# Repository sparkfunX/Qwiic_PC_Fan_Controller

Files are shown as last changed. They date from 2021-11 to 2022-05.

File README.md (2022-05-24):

Qwiic PC Fan Controller
========================================

Qwiic PC Fan Controller

[*Qwiic PC Fan Controller (SPX-18570)*](https://www.sparkfun.com/products/18570)

Whether for active cooling or ventilation, a tiny fan can make a big difference. And by that logic a big fan can make an even bigger difference! Luckily, 4-Wire PC cooling fans come in all shapes and sizes, so there's definitely one out there that's perfect for your project. The only downside is that they can be a pain to drive if you don't need them to be 100% on the throttle all the time. To remedy this, we've modified our Qwiic Blower Fan board to drive any 3- or 4-wire PC Fan with any voltage from 5 to 20VDC!

The Qwiic PC Fan Controller allows you easily control almost any PC fan over the Qwiic bus using the on board ATtiny microcontroller and control firmware. The control firmware monitors the tachometer output of the fan in order to implement PI Control over the fan speed, allowing you to set your desired speed in real units. It's also possible to disable the PI control loop and set the speed as a proportion of the maximum. The accompanying Arduino library includes example code for controlling the fan, tweaking settings, and even setting the fan speed based on an attached Qwiic Temperature Sensor and a lookup table. The on board trimpots allow you to very quickly tune the PI loop parameters to your application, but they can also be overridden by the Qwiic bus for remote configuration.

Heads Up! Without any external power supply connected, the Qwiic PC Fan Controller will attempt to drive the connected fan from the Qwiic bus. Even a very small 5V fan operates at the upper limit of the Qwiic bus' power delivery capability. If there are few other devices on the bus and the fan is not allowed to rapidly change throttle, it is possible to power a small fan directly from the bus. In most applications, however, it will be necessary to provide the PC Fan Controller with a dedicated fan power supply.

Repository Contents
-------------------

* **/Firmware** - Control firmware for the ATtiny
* **/Hardware** - Eagle design files (.brd, .sch)
* **/Production** - Panelized hardware files for production

License Information
-------------------

This product is _**open source**_! 

Please review the LICENSE.md file for license information. 

If you have any questions or concerns on licensing, please contact technical support on our [SparkFun forums](https://forum.sparkfun.com/viewforum.php?f=152).

Distributed as-is; no warranty is given.

- Your friends at SparkFun.

_<COLLABORATION CREDIT>_

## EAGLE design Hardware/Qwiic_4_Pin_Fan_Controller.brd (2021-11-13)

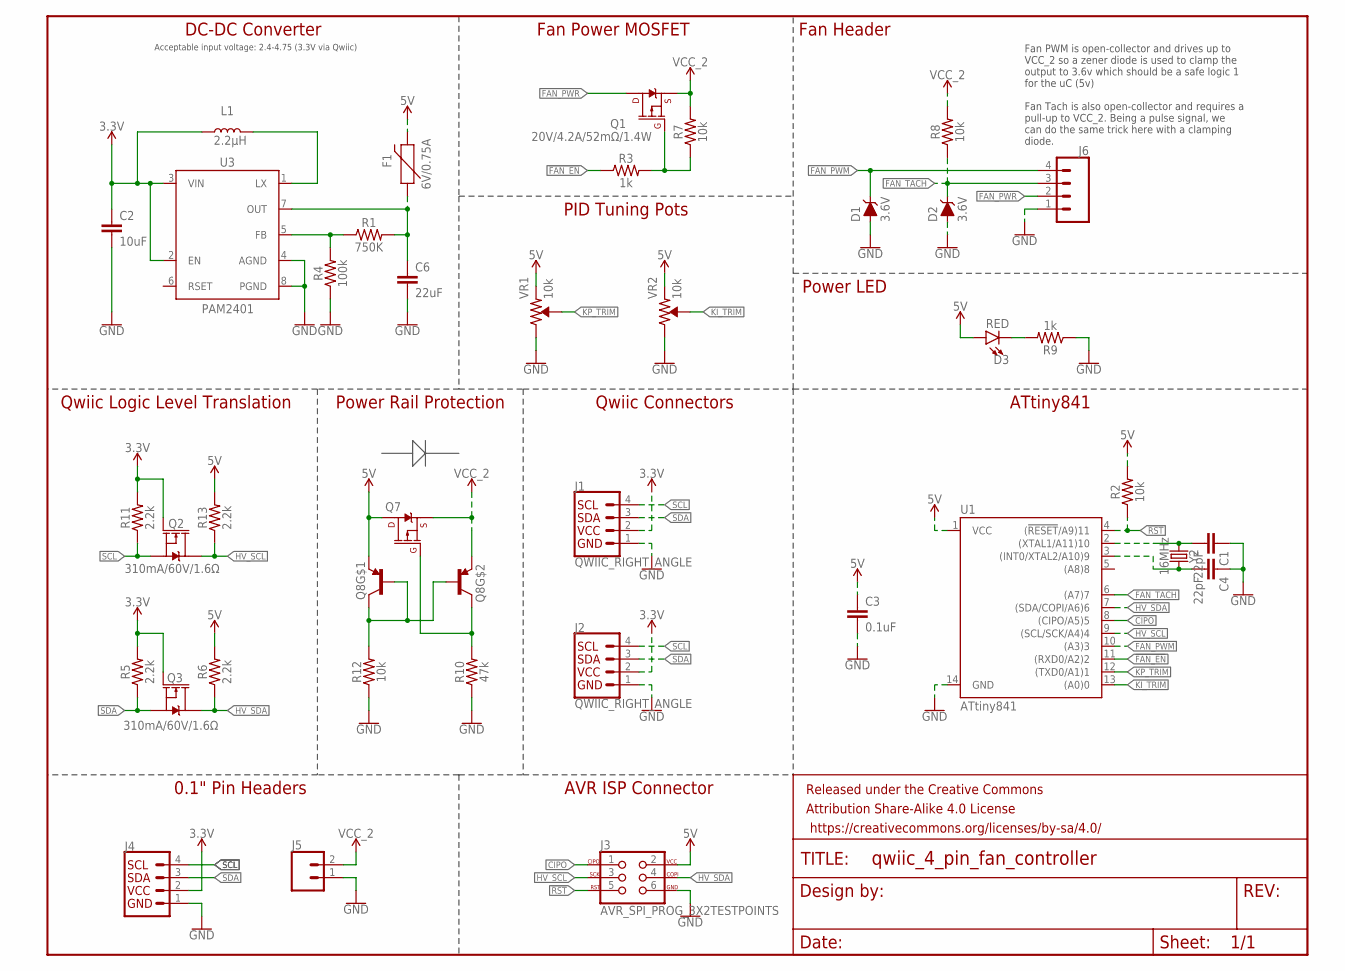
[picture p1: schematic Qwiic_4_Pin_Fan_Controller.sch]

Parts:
C1, C4: 22pF; 0603
C2: 10uF; 0603
C3: 0.1uF; 0603
C6: 22uF; 0805
D1, D2: 3.6V; SOD-323
D3: RED; LED-0603
F1: 6V/0.75A; 1206
FRAME1: FRAME-LETTER; CREATIVE_COMMONS
J1, J2: QWIIC_RIGHT_ANGLE; JST04_1MM_RA
J3: AVR_SPI_PROG_3X2TESTPOINTS; 2X3_TEST_POINTS
J4: I2C_STANDARD_NO_SILK; 1X04_NO_SILK
J5: CONN_021X02_NO_SILK; 1X02_NO_SILK
J6: CONN_041X04_NO_SILK; 1X04_NO_SILK
L1: 2.2μH; 0806
Q1, Q7: 20V/4.2A/52mΩ/1.4W; SOT23-3
Q2, Q3: 310mA/60V/1.6Ω; SOT323
Q8: TRANS_PNP_DUALSOT-363; SOT363_PHILIPS
R1: 750K; 0603
R2, R7, R8, R12: 10k; 0603@1
R3, R9: 1k; 0603
R4: 100k; 0603
R5, R6, R11, R13: 2.2k; 0603
R10: 47k; 0603@1
U1: ATtiny841; SO14
U3: PAM2401; MSOP8
VR1, VR2: 10k; TRIMPOT-SMD-3MM-CLOSED
Y2: 16MHz; CRYSTAL-SMD-2.0X1.6MM

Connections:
3.3V: C2.1, J1.2, J2.2, J4.2, L1.1, Q2.1 (G), Q3.1 (G), R5.2, R11.2, U3.2 (EN), U3.3 (VIN)
5V: C3.1, D3.A, F1.2, J3.2, Q7.3 (D), Q8.1 (E), R2.2, R6.2, R13.2, U1.1 (VCC), VR1.1 (CCW), VR2.1 (CCW)
!FAN_EN: R3.1, U1.11 ((RXD0/A2)2)
!RST: J3.5, R2.1, U1.4 ((!RESET!/A9)11)
CIPO: J3.1, U1.8 ((CIPO/A5)5)
FAN_PWM: D1.C, J6.4, U1.10 ((A3)3)
FAN_PWR: J6.2, Q1.3 (D)
FAN_TACH: D2.C, J6.3, R8.1, U1.6 ((A7)7)
GND: C1.1, C2.2, C3.2, C4.1, C6.2, D1.A, D2.A, J1.1, J2.1, J3.6, J4.1, J5.1, J6.1, R4.1, R9.1, R10.1, R12.1, U1.14 (GND), U3.4 (AGND), U3.8 (PGND), VR1.3 (CW), VR2.3 (CW)
HV_SCL: J3.3, Q2.3 (D), R13.1, U1.9 ((SCL/SCK/A4)4)
HV_SDA: J3.4, Q3.3 (D), R6.1, U1.7 ((SDA/COPI/A6)6)
KI_TRIM: U1.13 ((A0)0), VR2.2 (WIPER)
KP_TRIM: U1.12 ((TXD0/A1)1), VR1.2 (WIPER)
unnamed: C4.2, U1.3 ((INT0/XTAL2/A10)9), Y2.1
unnamed: R1.1, R4.2, U3.5 (FB)
unnamed: L1.2, U3.1 (LX)
unnamed: C1.2, U1.2 ((XTAL1/A11)10), Y2.3 (2)
unnamed: Q1.1 (G), R3.2, R7.1
unnamed: C6.1, F1.1, R1.2, U3.7 (OUT)
unnamed: D3.C, R9.2
unnamed: Q7.1 (G), Q8.3 (C), R10.2
unnamed: Q8.2 (B), Q8.5 (B), Q8.6 (C), R12.2
SCL: J1.4, J2.4, J4.4, Q2.2 (S), R11.1
SDA: J1.3, J2.3, J4.3, Q3.2 (S), R5.1
VCC_2: J5.2, Q1.2 (S), Q7.2 (S), Q8.4 (E), R7.2, R8.2

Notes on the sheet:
DC-DC Converter
Acceptable input voltage: 2.4-4.75 (3.3V via Qwiic)
ATtiny841
Qwiic Connectors
Qwiic Logic Level Translation
0.1" Pin Headers
AVR ISP Connector
Fan Power MOSFET
Fan Header
Fan PWM is open-collector and drives up to VCC_2 so a zener diode is used to clamp the output to 3.6v which should be a safe logic 1 for the uC (5v) Fan Tach is also open-collector and requires a pull-up to VCC_2. Being a pulse signal, we can do the same trick here with a clamping diode.
PID Tuning Pots
Power LED
Power Rail Protection

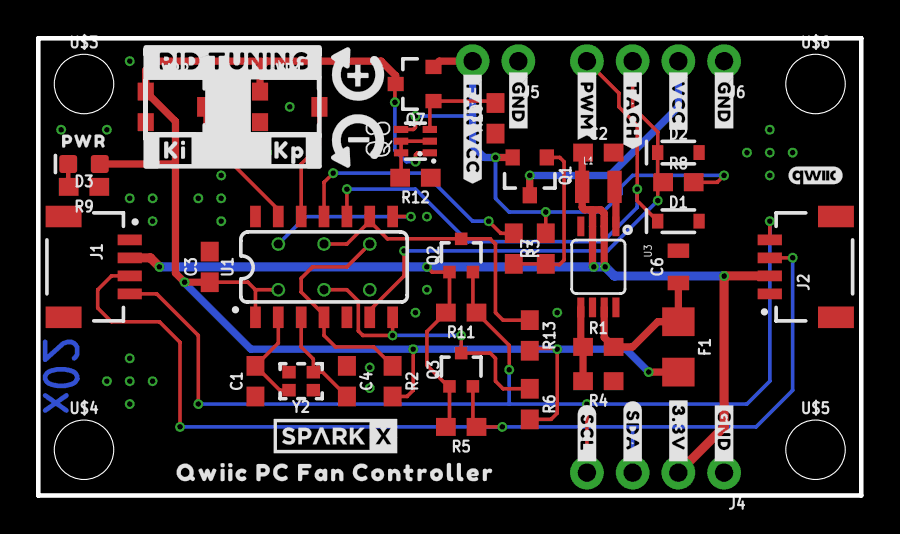
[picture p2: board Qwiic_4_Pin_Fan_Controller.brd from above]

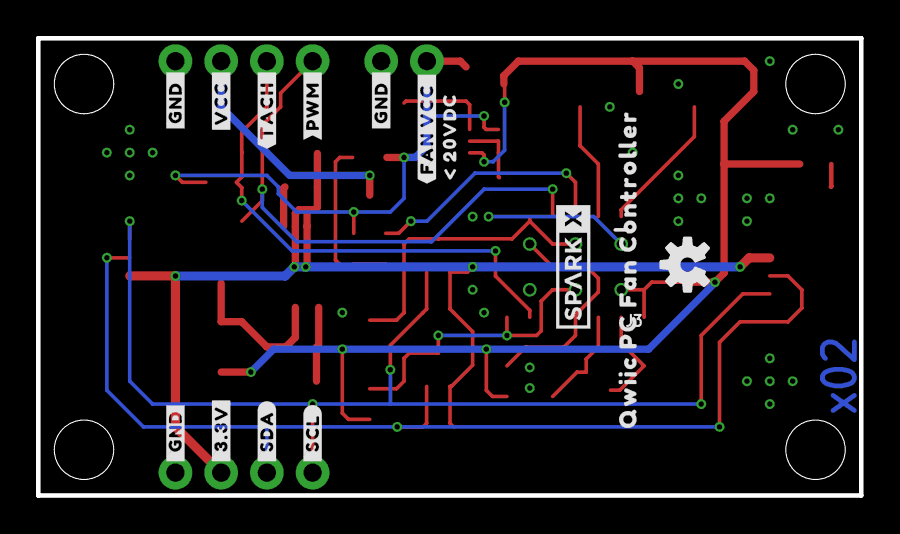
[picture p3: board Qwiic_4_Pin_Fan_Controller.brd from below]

Board: 2 copper layers, 45.7 x 25.4 mm, 76 parts (15 on the bottom side), 25 nets.

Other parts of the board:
U$1, U$9, U$21: #_GND#0
U$2: #_VCC#0
U$3, U$4, U$5, U$6: STAND-OFF
U$7: #_TACH#0
U$8: #_PWM#0
U$10, U$20, U$26: #GND_#0
U$11: #3#3V_#0
U$12: #SDA_#0
U$13: #SCL_#0
U$14: #PID_TUNING0
U$15: KI0
U$16: KP0
U$17: QWIIC_3MM
U$18, U$36: SPARKX-SMALL
U$19: #_FAN_VCC#0
U$22: PWR0
U$23: #VCC_#0
U$24: #TACH_#0
U$25: #PWM_#0
U$27: #_3#3V#0
U$28: #_SDA#0
U$29: #_SCL#0
U$30, U$35: QWIIC_PC_FAN_CONTROLLER0
U$31: #FAN_VCC_#0
U$32: _#_20VDC0
U$37: OSHW-LOGO-S
U$38: TURN_INDICATOR#SVG0

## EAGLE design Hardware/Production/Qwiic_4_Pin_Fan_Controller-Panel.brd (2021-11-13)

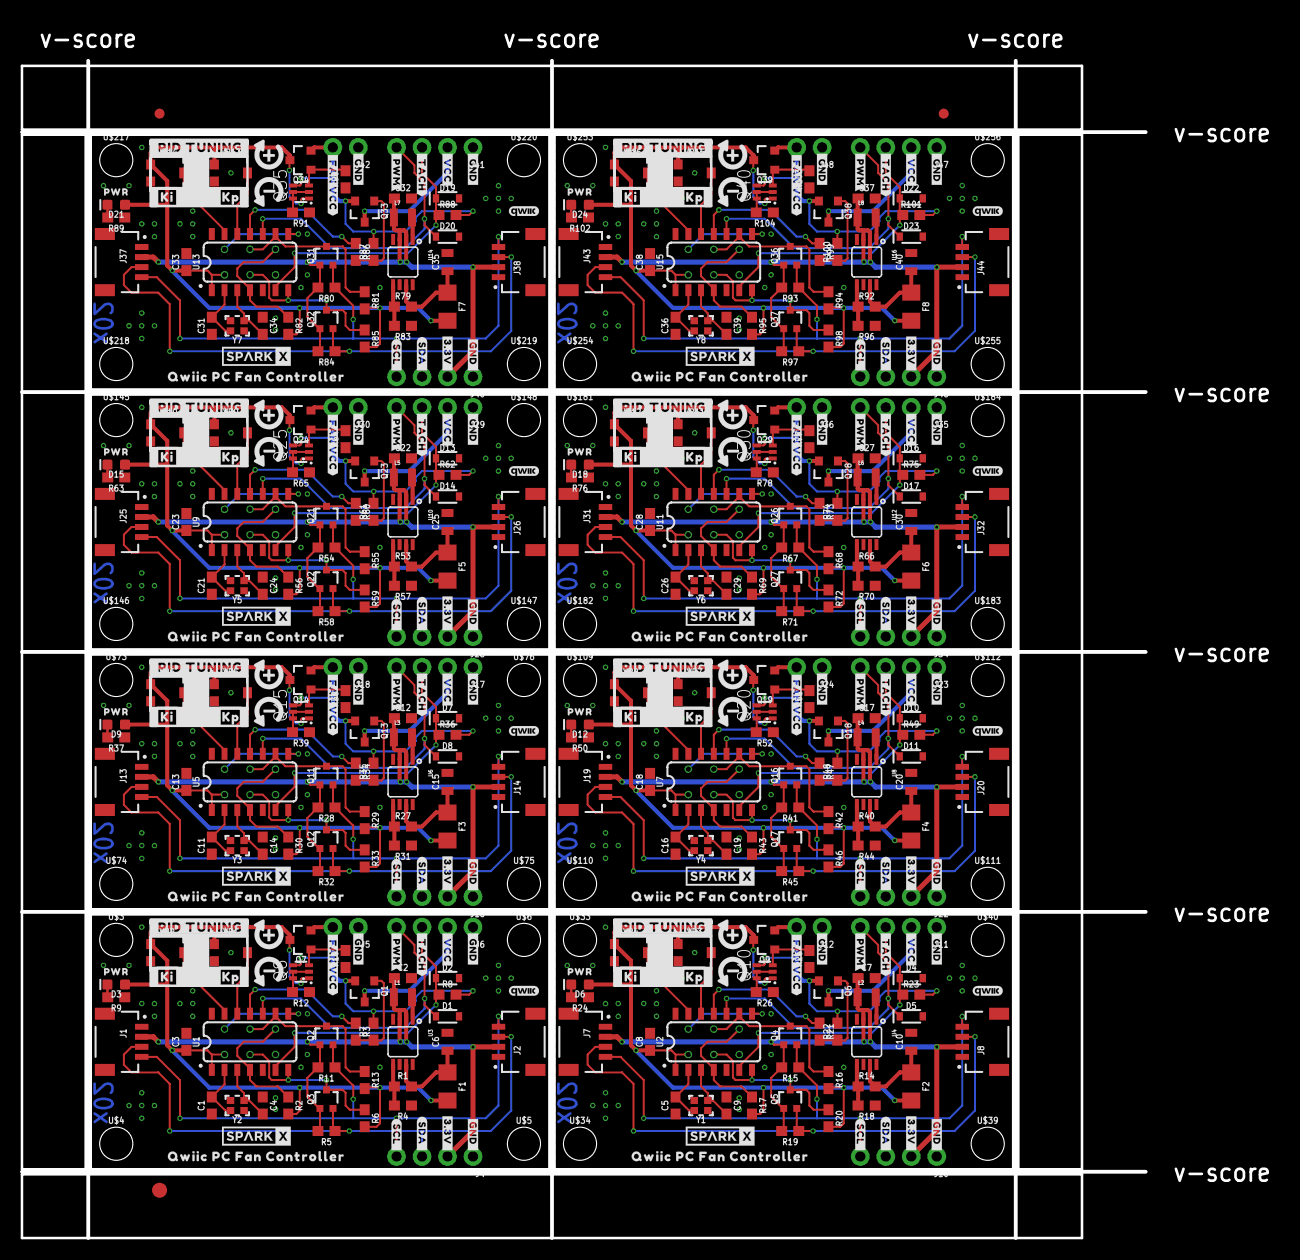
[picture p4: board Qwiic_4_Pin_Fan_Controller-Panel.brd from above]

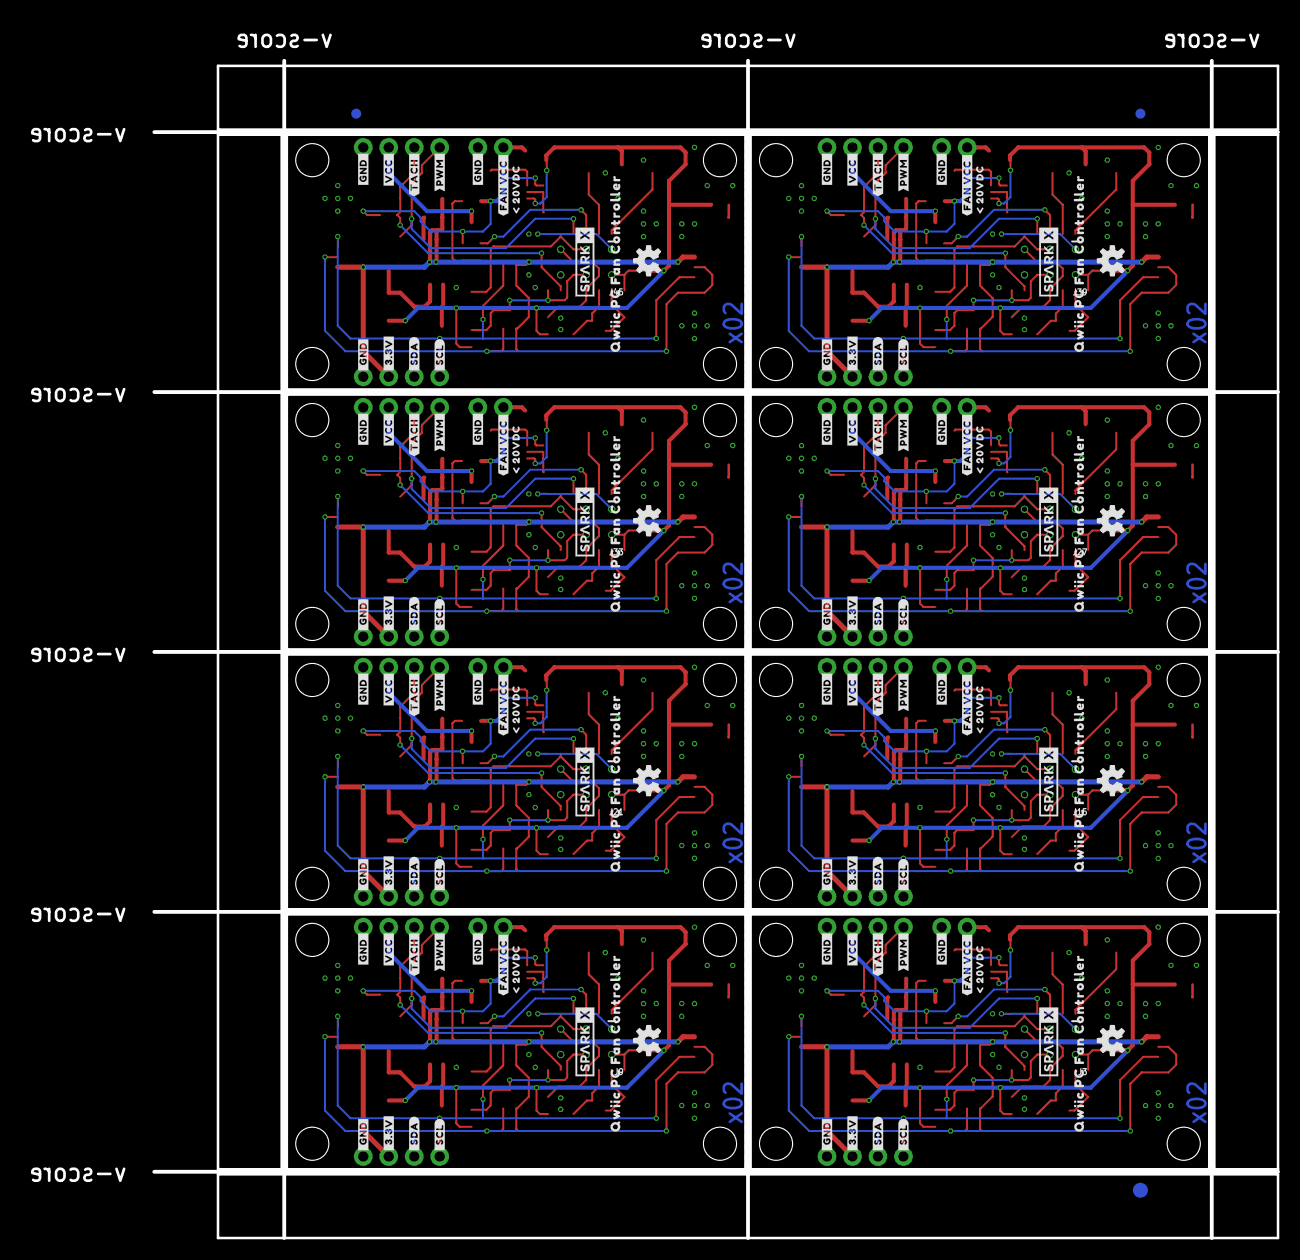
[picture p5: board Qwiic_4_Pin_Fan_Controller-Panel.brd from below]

Board: 2 copper layers, 112.0 x 117.3 mm, 606 parts (123 on the bottom side), 200 nets.

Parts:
C1, C4, C5, C9, C11, C14, C16, C19, C21, C24, C26, C29, C31, C34, C36, C39: 22pF; 0603
C2, C7, C12, C17, C22, C27, C32, C37: 10uF; 0603
C3, C8, C13, C18, C23, C28, C33, C38: 0.1uF; 0603
C6, C10, C15, C20, C25, C30, C35, C40: 22uF; 0805
D1, D2, D4, D5, D7, D8, D10, D11, D13, D14, D16, D17, D19, D20, D22, D23: 3.6V; SOD-323
D3, D6, D9, D12, D15, D18, D21, D24: RED; LED-0603
E$1, E$2, E$3, E$4: FIDUCIAL-1X2
E$5, E$6: FIDUCIAL-1.5X3
F1, F2, F3, F4, F5, F6, F7, F8: 6V/0.75A; 1206
J1, J2, J7, J8, J13, J14, J19, J20, J25, J26, J31, J32, J37, J38, J43, J44: QWIIC_RIGHT_ANGLE; JST04_1MM_RA
J3, J9, J15, J21, J27, J33, J39, J45: AVR_SPI_PROG_3X2TESTPOINTS; 2X3_TEST_POINTS
J4, J6, J10, J11, J16, J17, J22, J23, J28, J29, J34, J35, J40, J41, J46, J47: 1X04_NO_SILK
J5, J12, J18, J24, J30, J36, J42, J48: 1X02_NO_SILK
L1, L2, L3, L4, L5, L6, L7, L8: 2.2μH; 0806
Q1, Q6, Q7, Q9, Q13, Q14, Q18, Q19, Q23, Q24, Q28, Q29, Q33, Q34, Q38, Q39: 20V/4.2A/52mΩ/1.4W; SOT23-3
Q2, Q3, Q4, Q5, Q11, Q12, Q16, Q17, Q21, Q22, Q26, Q27, Q31, Q32, Q36, Q37: 310mA/60V/1.6Ω; SOT323
Q8, Q10, Q15, Q20, Q25, Q30, Q35, Q40: SOT363_PHILIPS
R1, R14, R27, R40, R53, R66, R79, R92: 750K; 0603
R2, R7, R8, R12, R17, R22, R23, R26, R30, R35, R36, R39, R43, R48, R49, R52, R56, R61, R62, R65, R69, R74, R75, R78, R82, R87, R88, R91, R95, R100, R101, R104: 10k; 0603@1
R3, R9, R21, R24, R34, R37, R47, R50, R60, R63, R73, R76, R86, R89, R99, R102: 1k; 0603
R4, R18, R31, R44, R57, R70, R83, R96: 100k; 0603
R5, R6, R11, R13, R15, R16, R19, R20, R28, R29, R32, R33, R41, R42, R45, R46, R54, R55, R58, R59, R67, R68, R71, R72, R80, R81, R84, R85, R93, R94, R97, R98: 2.2k; 0603
R10, R25, R38, R51, R64, R77, R90, R103: 47k; 0603@1
U1, U2, U5, U7, U9, U11, U13, U15: ATtiny841; SO14
U3, U4, U6, U8, U10, U12, U14, U16: PAM2401; MSOP8
U$1, U$9, U$21, U$41, U$45, U$53, U$77, U$81, U$89, U$113, U$117, U$125, U$149, U$153, U$161, U$185, U$189, U$197, U$221, U$225, U$233, U$257, U$261, U$269: #_GND#0
U$2, U$42, U$78, U$114, U$150, U$186, U$222, U$258: #_VCC#0
U$3, U$4, U$5, U$6, U$33, U$34, U$39, U$40, U$73, U$74, U$75, U$76, U$109, U$110, U$111, U$112, U$145, U$146, U$147, U$148, U$181, U$182, U$183, U$184, U$217, U$218, U$219, U$220, U$253, U$254, U$255, U$256: STAND-OFF
U$7, U$43, U$79, U$115, U$151, U$187, U$223, U$259: #_TACH#0
U$8, U$44, U$80, U$116, U$152, U$188, U$224, U$260: #_PWM#0
U$10, U$20, U$26, U$46, U$52, U$57, U$82, U$88, U$93, U$118, U$124, U$129, U$154, U$160, U$165, U$190, U$196, U$201, U$226, U$232, U$237, U$262, U$268, U$273: #GND_#0
U$11, U$47, U$83, U$119, U$155, U$191, U$227, U$263: #3#3V_#0
U$12, U$48, U$84, U$120, U$156, U$192, U$228, U$264: #SDA_#0
U$13, U$49, U$85, U$121, U$157, U$193, U$229, U$265: #SCL_#0
U$14, U$66, U$102, U$138, U$174, U$210, U$246, U$282: #PID_TUNING0
U$15, U$67, U$103, U$139, U$175, U$211, U$247, U$283: KI0
U$16, U$68, U$104, U$140, U$176, U$212, U$248, U$284: KP0
U$17, U$50, U$86, U$122, U$158, U$194, U$230, U$266: QWIIC_3MM
U$18, U$36, U$51, U$62, U$87, U$98, U$123, U$134, U$159, U$170, U$195, U$206, U$231, U$242, U$267, U$278: SPARKX-SMALL
U$19, U$65, U$101, U$137, U$173, U$209, U$245, U$281: #_FAN_VCC#0
U$22, U$69, U$105, U$141, U$177, U$213, U$249, U$285: PWR0
U$23, U$54, U$90, U$126, U$162, U$198, U$234, U$270: #VCC_#0
U$24, U$55, U$91, U$127, U$163, U$199, U$235, U$271: #TACH_#0
U$25, U$56, U$92, U$128, U$164, U$200, U$236, U$272: #PWM_#0
U$27, U$58, U$94, U$130, U$166, U$202, U$238, U$274: #_3#3V#0
U$28, U$59, U$95, U$131, U$167, U$203, U$239, U$275: #_SDA#0
U$29, U$60, U$96, U$132, U$168, U$204, U$240, U$276: #_SCL#0
U$30, U$35, U$61, U$63, U$97, U$99, U$133, U$135, U$169, U$171, U$205, U$207, U$241, U$243, U$277, U$279: QWIIC_PC_FAN_CONTROLLER0
U$31, U$71, U$107, U$143, U$179, U$215, U$251, U$287: #FAN_VCC_#0
U$32, U$72, U$108, U$144, U$180, U$216, U$252, U$288: _#_20VDC0
U$37, U$64, U$100, U$136, U$172, U$208, U$244, U$280: OSHW-LOGO-S
U$38, U$70, U$106, U$142, U$178, U$214, U$250, U$286: TURN_INDICATOR#SVG0
VR1, VR2, VR3, VR4, VR5, VR6, VR7, VR8, VR9, VR10, VR11, VR12, VR13, VR14, VR15, VR16: 10k; TRIMPOT-SMD-3MM-CLOSED
Y1, Y2, Y3, Y4, Y5, Y6, Y7, Y8: 16MHz; CRYSTAL-SMD-2.0X1.6MM

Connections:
3.3V: C2.1, J1.2, J2.2, J4.2, L1.1, Q2.1, Q3.1, R5.2, R11.2, U3.2, U3.3
3.3V1: C7.1, J7.2, J8.2, J10.2, L2.1, Q4.1, Q5.1, R15.2, R19.2, U4.2, U4.3
3.3V2: C12.1, J13.2, J14.2, J16.2, L3.1, Q11.1, Q12.1, R28.2, R32.2, U6.2, U6.3
3.3V3: C17.1, J19.2, J20.2, J22.2, L4.1, Q16.1, Q17.1, R41.2, R45.2, U8.2, U8.3
3.3V4: C22.1, J25.2, J26.2, J28.2, L5.1, Q21.1, Q22.1, R54.2, R58.2, U10.2, U10.3
3.3V5: C27.1, J31.2, J32.2, J34.2, L6.1, Q26.1, Q27.1, R67.2, R71.2, U12.2, U12.3
3.3V6: C32.1, J37.2, J38.2, J40.2, L7.1, Q31.1, Q32.1, R80.2, R84.2, U14.2, U14.3
3.3V7: C37.1, J43.2, J44.2, J46.2, L8.1, Q36.1, Q37.1, R93.2, R97.2, U16.2, U16.3
5V: C3.1, D3.A, F1.2, J3.2, Q7.3, Q8.1, R2.2, R6.2, R13.2, U1.1, VR1.1, VR2.1
5V1: C8.1, D6.A, F2.2, J9.2, Q9.3, Q10.1, R16.2, R17.2, R20.2, U2.1, VR3.1, VR4.1
5V2: C13.1, D9.A, F3.2, J15.2, Q14.3, Q15.1, R29.2, R30.2, R33.2, U5.1, VR5.1, VR6.1
5V3: C18.1, D12.A, F4.2, J21.2, Q19.3, Q20.1, R42.2, R43.2, R46.2, U7.1, VR7.1, VR8.1
5V4: C23.1, D15.A, F5.2, J27.2, Q24.3, Q25.1, R55.2, R56.2, R59.2, U9.1, VR9.1, VR10.1
5V5: C28.1, D18.A, F6.2, J33.2, Q29.3, Q30.1, R68.2, R69.2, R72.2, U11.1, VR11.1, VR12.1
5V6: C33.1, D21.A, F7.2, J39.2, Q34.3, Q35.1, R81.2, R82.2, R85.2, U13.1, VR13.1, VR14.1
5V7: C38.1, D24.A, F8.2, J45.2, Q39.3, Q40.1, R94.2, R95.2, R98.2, U15.1, VR15.1, VR16.1
!FAN_EN: R3.1, U1.11
!FAN_EN1: R21.1, U2.11
!FAN_EN2: R34.1, U5.11
!FAN_EN3: R47.1, U7.11
!FAN_EN4: R60.1, U9.11
!FAN_EN5: R73.1, U11.11
!FAN_EN6: R86.1, U13.11
!FAN_EN7: R99.1, U15.11
!RST: J3.5, R2.1, U1.4
!RST1: J9.5, R17.1, U2.4
!RST2: J15.5, R30.1, U5.4
!RST3: J21.5, R43.1, U7.4
!RST4: J27.5, R56.1, U9.4
!RST5: J33.5, R69.1, U11.4
!RST6: J39.5, R82.1, U13.4
!RST7: J45.5, R95.1, U15.4
CIPO: J3.1, U1.8
CIPO1: J9.1, U2.8
CIPO2: J15.1, U5.8
CIPO3: J21.1, U7.8
CIPO4: J27.1, U9.8
CIPO5: J33.1, U11.8
CIPO6: J39.1, U13.8
CIPO7: J45.1, U15.8
FAN_PWM: D1.C, J6.4, U1.10
FAN_PWM1: D5.C, J11.4, U2.10
FAN_PWM2: D8.C, J17.4, U5.10
FAN_PWM3: D11.C, J23.4, U7.10
FAN_PWM4: D14.C, J29.4, U9.10
FAN_PWM5: D17.C, J35.4, U11.10
FAN_PWM6: D20.C, J41.4, U13.10
FAN_PWM7: D23.C, J47.4, U15.10
FAN_PWR: J6.2, Q1.3
FAN_PWR1: J11.2, Q6.3
FAN_PWR2: J17.2, Q13.3
FAN_PWR3: J23.2, Q18.3
FAN_PWR4: J29.2, Q23.3
FAN_PWR5: J35.2, Q28.3
FAN_PWR6: J41.2, Q33.3
FAN_PWR7: J47.2, Q38.3
FAN_TACH: D2.C, J6.3, R8.1, U1.6
FAN_TACH1: D4.C, J11.3, R23.1, U2.6
FAN_TACH2: D7.C, J17.3, R36.1, U5.6
FAN_TACH3: D10.C, J23.3, R49.1, U7.6
FAN_TACH4: D13.C, J29.3, R62.1, U9.6
FAN_TACH5: D16.C, J35.3, R75.1, U11.6
FAN_TACH6: D19.C, J41.3, R88.1, U13.6
FAN_TACH7: D22.C, J47.3, R101.1, U15.6
GND: C1.1, C2.2, C3.2, C4.1, C6.2, D1.A, D2.A, J1.1, J2.1, J3.6, J4.1, J5.1, J6.1, R4.1, R9.1, R10.1, R12.1, U1.14, U3.4, U3.8, VR1.3, VR2.3
GND1: C5.1, C7.2, C8.2, C9.1, C10.2, D4.A, D5.A, J7.1, J8.1, J9.6, J10.1, J11.1, J12.1, R18.1, R24.1, R25.1, R26.1, U2.14, U4.4, U4.8, VR3.3, VR4.3
GND2: C11.1, C12.2, C13.2, C14.1, C15.2, D7.A, D8.A, J13.1, J14.1, J15.6, J16.1, J17.1, J18.1, R31.1, R37.1, R38.1, R39.1, U5.14, U6.4, U6.8, VR5.3, VR6.3
GND3: C16.1, C17.2, C18.2, C19.1, C20.2, D10.A, D11.A, J19.1, J20.1, J21.6, J22.1, J23.1, J24.1, R44.1, R50.1, R51.1, R52.1, U7.14, U8.4, U8.8, VR7.3, VR8.3
GND4: C21.1, C22.2, C23.2, C24.1, C25.2, D13.A, D14.A, J25.1, J26.1, J27.6, J28.1, J29.1, J30.1, R57.1, R63.1, R64.1, R65.1, U9.14, U10.4, U10.8, VR9.3, VR10.3
GND5: C26.1, C27.2, C28.2, C29.1, C30.2, D16.A, D17.A, J31.1, J32.1, J33.6, J34.1, J35.1, J36.1, R70.1, R76.1, R77.1, R78.1, U11.14, U12.4, U12.8, VR11.3, VR12.3
GND6: C31.1, C32.2, C33.2, C34.1, C35.2, D19.A, D20.A, J37.1, J38.1, J39.6, J40.1, J41.1, J42.1, R83.1, R89.1, R90.1, R91.1, U13.14, U14.4, U14.8, VR13.3, VR14.3
GND7: C36.1, C37.2, C38.2, C39.1, C40.2, D22.A, D23.A, J43.1, J44.1, J45.6, J46.1, J47.1, J48.1, R96.1, R102.1, R103.1, R104.1, U15.14, U16.4, U16.8, VR15.3, VR16.3
HV_SCL: J3.3, Q2.3, R13.1, U1.9
HV_SCL1: J9.3, Q4.3, R16.1, U2.9
HV_SCL2: J15.3, Q11.3, R29.1, U5.9
HV_SCL3: J21.3, Q16.3, R42.1, U7.9
HV_SCL4: J27.3, Q21.3, R55.1, U9.9
HV_SCL5: J33.3, Q26.3, R68.1, U11.9
HV_SCL6: J39.3, Q31.3, R81.1, U13.9
HV_SCL7: J45.3, Q36.3, R94.1, U15.9
HV_SDA: J3.4, Q3.3, R6.1, U1.7
HV_SDA1: J9.4, Q5.3, R20.1, U2.7
HV_SDA2: J15.4, Q12.3, R33.1, U5.7
HV_SDA3: J21.4, Q17.3, R46.1, U7.7
HV_SDA4: J27.4, Q22.3, R59.1, U9.7
HV_SDA5: J33.4, Q27.3, R72.1, U11.7
HV_SDA6: J39.4, Q32.3, R85.1, U13.7
HV_SDA7: J45.4, Q37.3, R98.1, U15.7
KI_TRIM: U1.13, VR2.2
KI_TRIM1: U2.13, VR4.2
KI_TRIM2: U5.13, VR6.2
KI_TRIM3: U7.13, VR8.2
KI_TRIM4: U9.13, VR10.2
KI_TRIM5: U11.13, VR12.2
KI_TRIM6: U13.13, VR14.2
KI_TRIM7: U15.13, VR16.2
KP_TRIM: U1.12, VR1.2
KP_TRIM1: U2.12, VR3.2
KP_TRIM2: U5.12, VR5.2
KP_TRIM3: U7.12, VR7.2
KP_TRIM4: U9.12, VR9.2
KP_TRIM5: U11.12, VR11.2
KP_TRIM6: U13.12, VR13.2
KP_TRIM7: U15.12, VR15.2
unnamed: C4.2, U1.3, Y2.1
unnamed: R1.1, R4.2, U3.5
unnamed: L1.2, U3.1
unnamed: C1.2, U1.2, Y2.3
unnamed: Q1.1, R3.2, R7.1
unnamed: C6.1, F1.1, R1.2, U3.7
unnamed: D3.C, R9.2
unnamed: R14.1, R18.2, U4.5
unnamed: L2.2, U4.1
unnamed: C9.2, U2.3, Y1.1
unnamed: C5.2, U2.2, Y1.3
unnamed: Q6.1, R21.2, R22.1
unnamed: C10.1, F2.1, R14.2, U4.7
unnamed: D6.C, R24.2
unnamed: Q7.1, Q8.3, R10.2
unnamed: Q8.2, Q8.5, Q8.6, R12.2
unnamed: Q9.1, Q10.3, R25.2
unnamed: Q10.2, Q10.5, Q10.6, R26.2
unnamed: R27.1, R31.2, U6.5
unnamed: L3.2, U6.1
unnamed: C14.2, U5.3, Y3.1
unnamed: C11.2, U5.2, Y3.3
unnamed: Q13.1, R34.2, R35.1
unnamed: C15.1, F3.1, R27.2, U6.7
unnamed: D9.C, R37.2
unnamed: Q14.1, Q15.3, R38.2
unnamed: Q15.2, Q15.5, Q15.6, R39.2
unnamed: R40.1, R44.2, U8.5
unnamed: L4.2, U8.1
unnamed: C19.2, U7.3, Y4.1
unnamed: C16.2, U7.2, Y4.3
unnamed: Q18.1, R47.2, R48.1
unnamed: C20.1, F4.1, R40.2, U8.7
unnamed: D12.C, R50.2
unnamed: Q19.1, Q20.3, R51.2
unnamed: Q20.2, Q20.5, Q20.6, R52.2
unnamed: R53.1, R57.2, U10.5
unnamed: L5.2, U10.1
unnamed: C24.2, U9.3, Y5.1
unnamed: C21.2, U9.2, Y5.3
unnamed: Q23.1, R60.2, R61.1
unnamed: C25.1, F5.1, R53.2, U10.7
unnamed: D15.C, R63.2
unnamed: Q24.1, Q25.3, R64.2
unnamed: Q25.2, Q25.5, Q25.6, R65.2
unnamed: R66.1, R70.2, U12.5
unnamed: L6.2, U12.1
unnamed: C29.2, U11.3, Y6.1
unnamed: C26.2, U11.2, Y6.3
unnamed: Q28.1, R73.2, R74.1
unnamed: C30.1, F6.1, R66.2, U12.7
unnamed: D18.C, R76.2
unnamed: Q29.1, Q30.3, R77.2
unnamed: Q30.2, Q30.5, Q30.6, R78.2
unnamed: R79.1, R83.2, U14.5
unnamed: L7.2, U14.1
unnamed: C34.2, U13.3, Y7.1
unnamed: C31.2, U13.2, Y7.3
unnamed: Q33.1, R86.2, R87.1
unnamed: C35.1, F7.1, R79.2, U14.7
unnamed: D21.C, R89.2
unnamed: Q34.1, Q35.3, R90.2
unnamed: Q35.2, Q35.5, Q35.6, R91.2
unnamed: R92.1, R96.2, U16.5
unnamed: L8.2, U16.1
unnamed: C39.2, U15.3, Y8.1
unnamed: C36.2, U15.2, Y8.3
unnamed: Q38.1, R99.2, R100.1
unnamed: C40.1, F8.1, R92.2, U16.7
unnamed: D24.C, R102.2
unnamed: Q39.1, Q40.3, R103.2
unnamed: Q40.2, Q40.5, Q40.6, R104.2
SCL: J1.4, J2.4, J4.4, Q2.2, R11.1
SCL1: J7.4, J8.4, J10.4, Q4.2, R15.1
SCL2: J13.4, J14.4, J16.4, Q11.2, R28.1
SCL3: J19.4, J20.4, J22.4, Q16.2, R41.1
SCL4: J25.4, J26.4, J28.4, Q21.2, R54.1
SCL5: J31.4, J32.4, J34.4, Q26.2, R67.1
SCL6: J37.4, J38.4, J40.4, Q31.2, R80.1
SCL7: J43.4, J44.4, J46.4, Q36.2, R93.1
SDA: J1.3, J2.3, J4.3, Q3.2, R5.1
SDA1: J7.3, J8.3, J10.3, Q5.2, R19.1
SDA2: J13.3, J14.3, J16.3, Q12.2, R32.1
SDA3: J19.3, J20.3, J22.3, Q17.2, R45.1
SDA4: J25.3, J26.3, J28.3, Q22.2, R58.1
SDA5: J31.3, J32.3, J34.3, Q27.2, R71.1
SDA6: J37.3, J38.3, J40.3, Q32.2, R84.1
SDA7: J43.3, J44.3, J46.3, Q37.2, R97.1
VCC_1: J12.2, Q6.2, Q9.2, Q10.4, R22.2, R23.2
VCC_2: J5.2, Q1.2, Q7.2, Q8.4, R7.2, R8.2
VCC_3: J18.2, Q13.2, Q14.2, Q15.4, R35.2, R36.2
VCC_4: J24.2, Q18.2, Q19.2, Q20.4, R48.2, R49.2
VCC_5: J30.2, Q23.2, Q24.2, Q25.4, R61.2, R62.2
VCC_6: J36.2, Q28.2, Q29.2, Q30.4, R74.2, R75.2
VCC_7: J42.2, Q33.2, Q34.2, Q35.4, R87.2, R88.2
VCC_8: J48.2, Q38.2, Q39.2, Q40.4, R100.2, R101.2

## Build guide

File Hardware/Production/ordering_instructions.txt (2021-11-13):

panel size, 106x117mm
PCB thickness, 1.6mm
number of layers, 2
soldermask color, Black
silkscreen color, White
oz copper, 1oz
finish, HASL lead free
stencils, none
pcs per panel, 8
min trace width, 0.2032mm / 0.0080in
min drill size, 0.3000mm / 0.0118in

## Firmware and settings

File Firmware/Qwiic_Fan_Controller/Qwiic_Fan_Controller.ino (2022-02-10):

#include <Wire.h>
#include <EEPROM.h>
#include <PIDController.h> // https://github.com/DonnyCraft1/PIDArduino

/****************************************************
 * HARDWARE CONFIGURATION
 * This firmware is used on multiple boards with minor
 * hardware differences so BE CAREFUL to define the 
 * correct hardware configuration below before 
 * programming!
****************************************************/
#define QWIIC_PC_FAN_CONTROLLER // SPX-18570
//#define QWIIC_BLOWER // SPX-18561

#ifdef QWIIC_PC_FAN_CONTROLLER
#define TRIM_DISABLE_DEFAULT 0x00
#endif
#ifdef QWIIC_BLOWER
#define TRIM_DISABLE_DEFAULT 0xFF
#endif 

/* PIN ASSIGNMENTS */
#define PIN_TRIM_KI 0    // ADC in from trimpot
#define PIN_TRIM_KP 1    // ADC in from trimpot
#define PIN_FAN_ENABLE 2 // DO to !FAN_EN
#define PIN_PWM_OUT 3    // DO to FAN_PWM
#define PIN_TACH_IN 7    // DI from FAN_TACH

/* I²C STUFF */
#define MAX_SENT_BYTES 0x05 // Used to ignore invalid commands
#define DEFAULT_ADDR 0x36   // Factory Default Peripheral Address

/* REGISTER MAP */
#define WIRE_ADDR 0x00             // Device Address
#define FAN_ENABLE 0x01            // Enable power to fan VCC pin (0xFF to enable)
#define SETPOINT_RPM 0x02          // PI Controller setpoint in RPM (2 bytes unsigned integer)
#define KP_VALUE 0x04              // PI Controller Proportional Term (2 bytes signed fixed decimal) \
                                   // Setting this parameter from the I²C Controller overrides the onboard trimpot
#define KI_VALUE 0x06              // PI Controller Integral Term (2 bytes signed fixed decimal) \
                                   // Setting this parameter from the I²C Controller overrides the onboard trimpot
#define FAN_TACH_DIVIDER 0x08      // Pulses per rotation indicated by fan/blower datasheet (usually 2)
#define FAN_ACTUAL_RPM 0x09        // Fan Speed Actual as indicated by Tachometer, input to PI Controller (2 bytes integer)
#define PI_OUT 0x0B                // Output of PI Controller for debugging (2 bytes integer)
#define PI_LOOP_DISABLE 0x0D       // Disable PI Controller and use contents of PROPORTIONAL_THROTTLE as speed (0xFF for Disable)
#define PROPORTIONAL_THROTTLE 0x0E // Fan speed as % of MAX. Inverse of PWM Width Cycle.                          \
                                   // When PI Controller is Enabled this register contains its output x (100/320) \
                                   // Whem PI Controller is Disabled the PWM Width Cycle is set to this register's inverse
#define TRIMMER_SCALE 0x0F         // Trimpot values are multiplied by this number. Probably only useful in edge cases. 2.0 (20) by default.
#define TRIMMER_DISABLE 0x10       // Stop reading trimpot ADCs and only use values written to the Kx_VALUE register by the I²C Controller (0xFF for Disable)
#define FW_VERSION 0x11            // Firmware version 

/* EEPROM MAP */
#define EEPROM_DEV_ADDR 0x00        // Because the I²C device address is user selectable, we need to remember it between boot cycles

/* MISCELLANEOUS GLOBAL VARS */
uint8_t receivedCommands[MAX_SENT_BYTES]; // I²C command buffer
uint8_t wire_addr = DEFAULT_ADDR;         // I²C device address
bool changeFlag = 0;                      // Use this flag to alert the main loop when a register change requires attention
uint8_t registerIndex = 0;                // Use this to track our position in the device registers during consecutive read operations

/****************************************************
 * SET THE REGISTER MAP DEFAULTS
 * These are the bus-accessible device registers
 * and their default values */
uint8_t registerMap[0x12] = 
    {
        0x00,                   // WIRE_ADDR
        0x00,                   // FAN_ENABLE
        0x00,                   // SETPOINT_RPM
        0x00,                   // SETPOINT_RPM BYTE 2
        0,                      // KP_VALUE (70 interpreted as 2.50)
        250,                     // KP_VALUE BYTE 2 
        1,                      // KP_VALUE (390 interpreted as 3.90)
        134,                     // KP_VALUE BYTE 2
        2,                   // FAN_TACH_DIVIDER (2 pulses per rotation)
        0x00,                   // FAN_ACTUAL_RPM 
        0x00,                   // FAN_ACTUAL_RPM BYTE 2
        0x00,                   // PI_OUT
        0x00,                   // PI_OUT BYTE 2
        0x00,                   // PI_LOOP_DISABLE (enabled)
        0x00,                   // PROPORTIONAL_THROTTLE
        20,                   // TRIMMER_SCALE (20 interpreted as 2.0)
        TRIM_DISABLE_DEFAULT,    // TRIMMER_DISABLE
        11                      // FIRMWARE VERSION 1.1
    };
/****************************************************/

// Instantiate PI Controller
PIDController piController;

void setup()
{
    // Check EEPROM for a bus address and set accordingly
    setWireAddress();

    // Setup timers for 25kHz Fast PWM
    fastPWMSetup();

    // Set the initial pin states
    pinMode(PIN_PWM_OUT, OUTPUT);
    pinMode(PIN_TACH_IN, INPUT_PULLUP); // Fan Tachometer is open-collector
    pinMode(PIN_FAN_ENABLE, OUTPUT);
    digitalWrite(PIN_FAN_ENABLE, HIGH); // Fan Enable is active low. Boot disabled to avoid hard start
    pinMode(PIN_TRIM_KI, INPUT);
    pinMode(PIN_TRIM_KP, INPUT);

    // Start I2C
    Wire.begin(wire_addr);
    Wire.onRequest(requestEvent);
    Wire.onReceive(receiveEvent);

    // Start the PI Controller
    piController.begin();
    piController.limit(20, 320); // Limit the PI output to prevent integral windup
}

void loop()
{
    // Get the tachometer reading, turn it into a real RPM using the value from
    // FAN_TACH_DIVIDER, and stuff it into FAN_ACTUAL_RPM for the I²C controller
    // to query and for the PI controller to compute against.
    readTachometer();

    // Finding which device register has been changed and updating
    // the approptiate settings takes some time so we only do it if
    // the registers have been poked. This way, we interfere as little
    // as possible with the PI Controller and PWM Generator
    if (changeFlag)
    {
        updateSettings();
    }

    // If the hardware is a Qwiic 4-Wire Fan Controller and the TRIMMER_DISABLE flag isn't set
    // then read the trimmers, apply the correct scale and offset, and then load those
    // values into the Kx_VALUE registers. If the TRIMMER_DISABLE flag is set, or this is
    // a Qwiic Blower board without trimpots, we skip reading the trimpots, so whatever
    // value is in the Kx_VALUE register from the last I²C receive is used for tuning.
    if (registerMap[TRIMMER_DISABLE] != 0xFF)
    {
        readTrimmers();
    }

    // Check whether the user has disabled the control loop in
    // favor of direct proportional speed control. If so, set
    // the PWM Width according to the contents of PROPORTIONAL_THROTTLE
    // if not, compute the output of the PI controller from the
    // contents of SETPOINT_RPM
    if (registerMap[PI_LOOP_DISABLE] == 0xFF)
    {
        pwmWidth(map(registerMap[PROPORTIONAL_THROTTLE], 0, 100, 0, 320));
    }
    else
    {
        piUpdate();
    }
}

/****************************************************
 * Function piUpdate()
 * The PID library has a 'compute' function, which we do
 * call in this method. However, in our particular case, 
 * it's easier to package that up with the tuning functions
 * becuase we always update our tunings before calculating 
 * the output. It seems excessive but it costs us less time
 * to just update the tunings than it does to check whether
 * it's necessary. We also use this method to update the
 * output value in the register map. 
****************************************************/
void piUpdate()
{

    float proportional = 0;
    float integral = 0;
    uint16_t setpoint = 0;
    uint16_t piOutput = 0;
    uint16_t tachReading = 0;

    // Expand the registerMap values back into int16
    // Multiply by 0.01 as neccessary to move the decimal into
    // the right position
    proportional += registerMap[KP_VALUE] << 8;
    proportional += registerMap[KP_VALUE + 0x01];
    proportional *= 0.01;

    integral += registerMap[KI_VALUE] << 8;
    integral += registerMap[KI_VALUE + 0x01];
    integral *= 0.01;

    setpoint += registerMap[SETPOINT_RPM] << 8;
    setpoint += registerMap[SETPOINT_RPM + 0x01];

    tachReading += registerMap[FAN_ACTUAL_RPM] << 8;
    tachReading += registerMap[FAN_ACTUAL_RPM + 0x01];

    // PC Fans tend to have a dead zone at the low end, so we limit the PI controller
    // to the range above this dead zone (to prevent stalling the fan and setting up
    // an oscillation) This does mean, however, that the PI controller will never 
    // organically output a 0, so if the fan speed is set to 0 we need to override the
    // PI controller
    if(setpoint !=0){

      // Update the PI Controller
      piController.setpoint(setpoint);
      piController.tune(proportional, integral, 0);
      piOutput = piController.compute(tachReading);

    }else{

      piOutput = 0;
      
    }

    // Update the PI_OUT register entry
    registerMap[PI_OUT] = piOutput >> 8;
    registerMap[PI_OUT + 0x01] = piOutput;

    // Actually set the fan PWM output
    pwmWidth(piOutput);
}

/****************************************************
 * Function readTrimmerAndTune()
 * Read the Trimpots, process them according to the 
 * scaling and offset registers, constrain them to 
 * the size of the Kx_VALUE registers, and store 
 * them for reference when tuning the PI Controller
****************************************************/
void readTrimmers()
{

    // Read ADCs into some temp vars
    // The data types are a little weird because of trying to make them
    // as small as possible for I²C transmission. This results in some
    // funny float math
    float ADCKP = analogRead(PIN_TRIM_KP) * 0.01; // Range 0 - 10.24
    float ADCKI = analogRead(PIN_TRIM_KI) * 0.01; // Range 0 - 10.24

    // Multiply by the scaling value from Kx_TRIM_SCALING
    // Use reinterpret_cast to ensure our int8 is correctly extracted from uint8 registerMap[]
    ADCKP *= static_cast<int8_t>(registerMap[TRIMMER_SCALE]) * 0.1; // Range -12.8 to 12.7
    ADCKI *= static_cast<int8_t>(registerMap[TRIMMER_SCALE]) * 0.1; // Range -12.8 to 12.7

    // ADCKx could very well be too large for int16 Kx_VALUE but because we used the correct
    // precision in all of the math up until now, we can simply truncate the result and all
    // we lose are a few decimals of precision that we don't want to store anyway
    registerMap[KP_VALUE] = int16_t(ADCKP * 100) >> 8;
    registerMap[KP_VALUE + 0x01] = int16_t(ADCKP * 100);
    registerMap[KI_VALUE] = int16_t(ADCKI * 100) >> 8;
    registerMap[KI_VALUE + 0x01] = int16_t(ADCKI * 100);
}

/****************************************************
 * Function updateSettings()
 * Check that our devicce settings still match those 
 * found in the register map. If not, change the device
 * settings then reset the change flag. 
 * This gets called every loop directly after a device 
 * register is written to. 
****************************************************/
void updateSettings()
{

    // Check if the device address has been changed
    // Compare against global var wire_addr which is
    // unchanged since last Wire.begin() call
    if ((registerMap[WIRE_ADDR] != wire_addr) && registerMap[WIRE_ADDR] > 0x07 && registerMap[WIRE_ADDR] < 0x78)
    {
        wire_addr = registerMap[WIRE_ADDR];
        // store the I²C Address in EEPROM so it sticks around on reboot
        EEPROM.put(EEPROM_DEV_ADDR, wire_addr);
        // restart I²C
        Wire.end();
        Wire.begin(wire_addr);
        Wire.onRequest(requestEvent);
        Wire.onReceive(receiveEvent);
    }else{
      registerMap[WIRE_ADDR] = wire_addr;
    }

    // The following are easy to evaluate and don't
    // touch EEPROM so we go ahead and "update" them
    // every time whether they've been changed or not

    // FAN ENABLE
    if (registerMap[FAN_ENABLE] == 0xFF)
    {
        digitalWrite(PIN_FAN_ENABLE, HIGH);
    }
    else
    {
        digitalWrite(PIN_FAN_ENABLE, LOW);
    }

    // Reset the flag
    changeFlag = 0;
}

/****************************************************
 * Function setWireAddress()
 * Check if there is a device address stored in EEPROM
 * If there is, set it. If not, store the factory default
 * and set that.
****************************************************/
void setWireAddress()
{
    uint8_t eepromVal;
    EEPROM.get(EEPROM_DEV_ADDR, eepromVal);
    if (eepromVal == 0xFF)
    {
        EEPROM.put(EEPROM_DEV_ADDR, DEFAULT_ADDR);
        registerMap[WIRE_ADDR] = DEFAULT_ADDR;
    }
    else
    {
        wire_addr = eepromVal;
        registerMap[WIRE_ADDR] = eepromVal;
    }
}

/****************************************************
 * Function readTachometer()
 * Read the pulse length of the Fan Tachometer and 
 * convert to real RPM. Cast to 2 bytes and store in 
 * appropriate register location
****************************************************/
void readTachometer()
{
    long tach; // Pulse length of tachometer pulse in microseconds
    long freq; // Frequency of tachometer pulse in Hz derived by (1000000 / pulse length in microseconds) / 2 transitions per pulse
    long rpm;  // RPM derived by (frequency / pulses per revolution) x 60

    tach = pulseIn(PIN_TACH_IN, LOW); // Get pulse length of tachometer pulse, from this we can derive the fan speed
    if(tach>0 && registerMap[FAN_TACH_DIVIDER] > 0){
      freq = 1000000 / tach / 2;
      rpm = (freq / registerMap[FAN_TACH_DIVIDER]) * 60;
    }else{
      rpm = 0;
    }

    registerMap[FAN_ACTUAL_RPM] = uint16_t(rpm) >> 8;
    registerMap[FAN_ACTUAL_RPM + 0x01] = uint16_t(rpm);
}

/****************************************************
 * Function fastPWMSetup()
 * Setup the appropriate timer registers on the Attiny841
 * to output FastPWM on OC1B, compare to ICR1 for TOP.
 * In FastPWM mode, TCNT1 will count up to TOP and then
 * reset. Output Compare is cleared when they match. 
****************************************************/
void fastPWMSetup()
{
    TCCR1B = 0; // Clear Timer Control Register 1B
    TCNT1 = 0;  // Clear Timer1

    TCCR1A &= ~_BV(WGM10); //FastPWM mode with ICR1
    TCCR1A |= _BV(WGM11);
    TCCR1A |= _BV(WGM12);
    TCCR1B |= _BV(WGM13);

    TCCR1A |= _BV(COM1B1); // Compare Output Mode Channel B (Non-Inverting Mode)
    TCCR1A &= ~_BV(COM1B0);

    TCCR1B |= _BV(CS10); // No Prescaler
    TCCR1B &= ~_BV(CS11);
    TCCR1B &= ~_BV(CS12);

    ICR1 = 320; //FastPWM mode counts up 320 (25kHz)
    OCR1B = 0;  //0-320 = 0-100% Width cycle
}

void pwmWidth(int width)
{
    // Change the width of the PWM wave generator
    // Maximum width is 320 cycles (100% duty)
    OCR1B = constrain(width, 0, 320);
    // Store the speed that we're setting the fan
    // as a proportion of the maximum (essentially
    // the inverse of the PWM duty cycle)
    registerMap[PROPORTIONAL_THROTTLE] = uint8_t(map(width, 0, 320, 0, 100));
}

/****************************************************
 * Function requestEvent()
 * Handle requests from the I²C controller
 * Emulate a proper I²C peripheral by writing out the 
 * contents of the last received register index and 
 * then increment the index for consecutive reads.
 * Register index is reset whenever new bytes are 
 * received so it can't run away.
****************************************************/
void requestEvent()
{
  for(uint8_t idx = registerIndex; idx < sizeof(registerMap); idx++)
  {
    Wire.write(registerMap[idx]);
  }
}

/****************************************************
 * Function receiveEvent(int bytesReceived)
 * Handle incoming bytes from I²C controller
****************************************************/
void receiveEvent(int bytesReceived)
{

    /* If we receive a single uint8_t, we can assume the controller is asking for the contents of a register 
   so we store the uint8_t in a global var that we can retreive during requestEvent() */

    for (int a = 0; a < bytesReceived; a++)
    {
        if (a < MAX_SENT_BYTES)
        {
            receivedCommands[a] = Wire.read(); //grab stuff and jam it into the command buffer
        }
        else
        {
            Wire.read(); //if we receive more data than allowed, chuck it
        }
    }

    if (bytesReceived == 1 && (receivedCommands[0] < sizeof(registerMap))) //if we got a uint8_t within the register map range, keep it
    {
        registerIndex = receivedCommands[0];
        return;
    }

    if (bytesReceived == 1 && (receivedCommands[0] >= sizeof(registerMap))) //if we got a uint8_t outside the register map range, chuck it
    {
        receivedCommands[0] = 0x00;
        registerIndex = 0x00;
        return;
    }

    /* If we receive multiple bytes, the first is a register address and the following 
    are values to write starting at the specified address */

    if (bytesReceived > 1)
    {
        // load received bytes into consecutive register addresses
        for (int i = 0; i < bytesReceived - 1; i++)
        {
            registerMap[(receivedCommands[0] + i)%sizeof(registerMap)] = receivedCommands[1 + i];
            
        }
        changeFlag = 1; // Set the change flag
    }

    return;
}

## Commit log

2021-07-19 x01 PCBs ordered
    [Qwiic_4_Pin_Fan_Controller-Panel.brd, Qwiic_4_Pin_Fan_Controller.brd, Qwiic_4_Pin_Fan_Controller.sch]
2021-10-17 Firmware too big
    Saving the combined firmware for posterity.
    It's 500bytes too big, so I'm gonna split it.
    [Qwiic_4_Pin_Fan_Controller-Panel.GBL, Qwiic_4_Pin_Fan_Controller-Panel.GBO, Qwiic_4_Pin_Fan_Controller-Panel.GBP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]
2021-10-21 Update Qwiic_4-Wire_Fan_Controller.ino
    Firmware works, doing some final PI tuning and writing the controller-side code
2021-10-25 Update Qwiic_4-Wire_Fan_Controller.ino
    Update to semifinal firmware
2021-10-27 Firmware Rename
    Making all naming consistent across Sparkle, Github, Arduino
2021-11-13 x02
    I exploded the proto by applying 12VDC without cutting the jumper.
    If I can do it, a customer _will_ do it.
    I've replaced the jumper with a mosfet "diode" protection circuit.
    [Qwiic_Fan_Controller.ino]
2021-11-13 x02 silk change and gerbers
    -Fix a silk label on the bottom
    -Panelize and CAM Production Files
    [Qwiic_4_Pin_Fan_Controller-Panel.GBL, Qwiic_4_Pin_Fan_Controller-Panel.GBO, Qwiic_4_Pin_Fan_Controller-Panel.GBS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]
2022-02-10 Move hardware files into hardware dir
    [Qwiic_4_Pin_Fan_Controller-Panel.GBL, Qwiic_4_Pin_Fan_Controller-Panel.GBO, Qwiic_4_Pin_Fan_Controller-Panel.GBP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]
2022-02-10 Updated Firmware
    - Firmware update pulled from Blower Fan
    - Add Compiled Binary from new firmware
    - Add Programming batch file with correct fuse bits
    [Qwiic_Fan_Controller.ino]

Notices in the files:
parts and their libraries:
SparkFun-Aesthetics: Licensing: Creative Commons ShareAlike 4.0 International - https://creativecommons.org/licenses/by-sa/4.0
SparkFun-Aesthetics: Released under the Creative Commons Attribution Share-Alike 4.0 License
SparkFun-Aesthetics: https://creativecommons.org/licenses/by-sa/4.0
